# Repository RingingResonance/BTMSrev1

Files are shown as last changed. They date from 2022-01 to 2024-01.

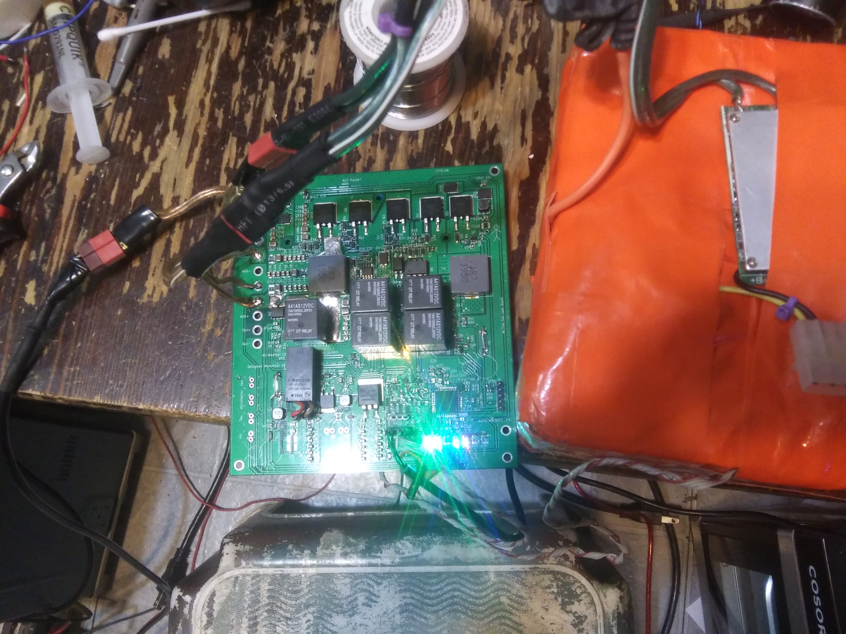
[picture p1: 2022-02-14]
pictures/20220212_222504.jpg

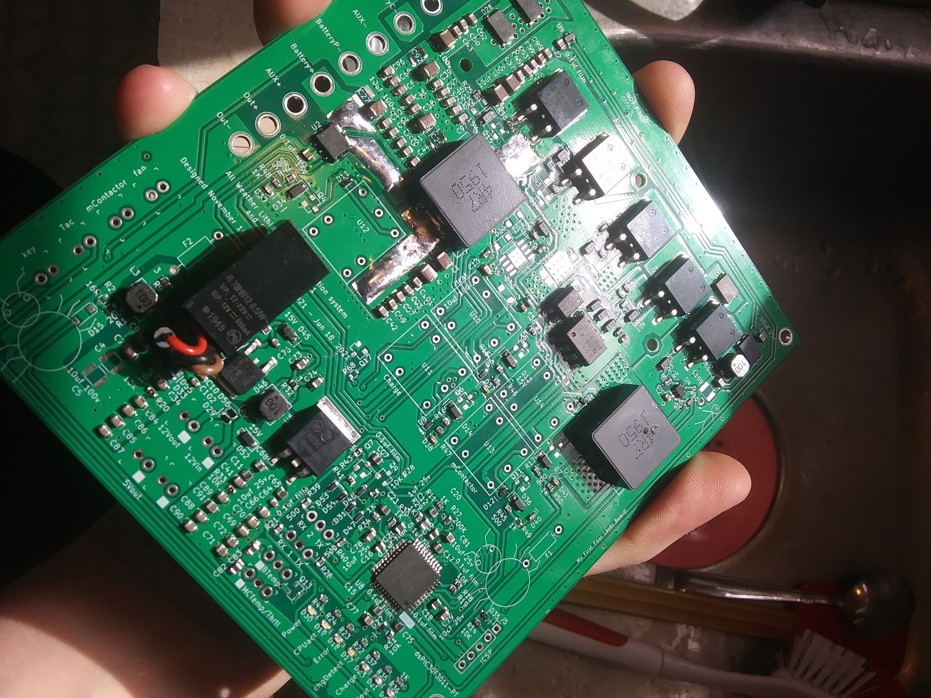
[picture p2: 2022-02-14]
pictures/20220122_115344.jpg

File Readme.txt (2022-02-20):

Battery Charge/Discharge and Heater Controller for small electric vehicles.

This system provides Battery telemetry services such as Voltage, Current, and Temperature. 

It also regulates charge/discharge voltages, limits current when battery temps are too high or too low, controls a battery heater for cold environments, and basic cooling fan control.
Works with lithium ion batteries, but does not provide cell ballancing. That must be done with a dedicated BMS.
The circuit provided should handle up to 30 amps with proper cooling. It also does basic error logging and will shut down the system on events such as under/over voltage, over current, temps out of range, internal CPU errors, etc. with room to expand.

At this time, Feb 19, 2022, Testing and verifying operation of circuit and firmware. System seems to be working as intended, but I'm still working on features and a few bugs here and there.

Heater circuit needs a higher current inductor to prevent smoke release.

Output side MOSFET drive circuit needs some fine tuning for effecientcy, but otherwise works and has been tested up to 1300 watts a few times on a 15min ride.

Charge circuit seems to work as intended, but all relays need bigger start capacitors, or better start circuits to succesfully latch.

Firmware needs display and monitoring routines written and reimplemented, and needs refactoring of several routines such as but not limited to the regulation routine for the purpose of saving code space, speed, and readability.

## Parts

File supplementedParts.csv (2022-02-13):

Index | Quantity | Part Number | Manufacturer Part Number | Description | Customer Reference | Available | Backorder | Unit Price | Extended Price USD
1 | 2 | 296-21435-5-ND | UCC27201D | IC GATE DRVR HALF-BRIDGE 8SOIC |  | 0 | 2 | 2.93000 | 5.86
2 | 10 | 846-BSS138BKWT106CT-ND | BSS138BKWT106 | NCH 60V 380MA, SOT-323, SMALL SI |  | 10 | 0 | 0.32600 | 3.26
3 | 4 | 1801-TSM3401CXRFGCT-ND | TSM3401CX RFG | MOSFET P-CHANNEL 30V 3A SOT23 |  | 4 | 0 | 0.58000 | 2.32
4 | 4 | VEMD10940FCT-ND | VEMD10940F | PHOTODIODE 790 TO 1050 NM |  | 4 | 0 | 0.40000 | 1.60
5 | 4 | ZXTP19020DFFCT-ND | ZXTP19020DFFTA | TRANS PNP 20V 5.5A SOT23F-3 |  | 4 | 0 | 0.83000 | 3.32
6 | 10 | 3757-BAS100AS-AU_R1_000A1CT-ND | BAS100AS-AU_R1_000A1 | SOD-123, SKY |  | 10 | 0 | 0.28500 | 2.85
7 | 5 | RNCF0603DTE16K0CT-ND | RNCF0603DTE16K0 | RES 16K OHM 0.5% 1/10W 0603 |  | 5 | 0 | 0.13000 | 0.65
8 | 5 | TSPB15U100SS1GCT-ND | TSPB15U100S S1G | DIODE SCHOTTKY 100V 15A SMPC4.0 |  | 5 | 0 | 1.71000 | 8.55

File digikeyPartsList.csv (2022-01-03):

Index | Quantity | Part Number | Manufacturer Part Number | Description | Customer Reference | Available | Backorder | Unit Price | Extended Price USD
1 | 17 | PCF1126CT-ND | ECP-U1C104MA5 | CAP FILM 0.1UF 20% 16VDC 0805 |  | 17 | 0 | 0.44500 | 7.57
2 | 10 | 1276-1102-1-ND | CL10A105KA8NNNC | CAP CER 1UF 25V X5R 0603 |  | 10 | 0 | 0.03400 | 0.34
3 | 17 | 490-16266-1-ND | GRM32EC72A106KE05L | CAP CER 10UF 100V X7S 1210 |  | 0 | 17 | 1.04000 | 17.68
4 | 30 | 490-10748-1-ND | GRM21BR61E106MA73L | CAP CER 10UF 25V X5R 0805 |  | 30 | 0 | 0.17200 | 5.16
5 | 1 | 490-10918-1-ND | GRJ21BC72A105KE11L | CAP CER 1UF 100V X7S 0805 |  | 1 | 0 | 0.46000 | 0.46
6 | 2 | 311-1523-1-ND | CC0603KRX7R0BB104 | CAP CER 0.1UF 100V X7R 0603 |  | 2 | 0 | 0.18000 | 0.36
7 | 50 | 490-10918-1-ND | GRJ21BC72A105KE11L | CAP CER 1UF 100V X7S 0805 |  | 50 | 0 | 0.22480 | 11.24
8 | 18 | DDZ15-7DICT-ND | DDZ15-7 | DIODE ZENER 15V 500MW SOD123 |  | 18 | 0 | 0.22300 | 4.01
9 | 5 | FSV20100VCT-ND | FSV20100V | DIODE SCHOTTKY 100V 20A TO277-3 |  | 0 | 5 | 1.46000 | 7.30
10 | 1 | VLMB1310-GS08CT-ND | VLMB1310-GS08 | LED BLUE 0603 SMD |  | 0 | 1 | 0.47000 | 0.47
11 | 1 | 732-4978-1-ND | 150060RS75000 | LED RED CLEAR 0603 SMD |  | 1 | 0 | 0.15000 | 0.15
12 | 1 | 1516-1055-1-ND | QBLP601-IG | LED GREEN CLEAR 0603 SMD |  | 1 | 0 | 0.40000 | 0.40
13 | 1 | 516-2486-1-ND | HSMA-C120 | LED AMBER CLEAR CHIP SMD R/A |  | 1 | 0 | 0.63000 | 0.63
14 | 1 | 516-2486-1-ND | HSMA-C120 | LED AMBER CLEAR CHIP SMD R/A |  | 1 | 0 | 0.63000 | 0.63
15 | 1 | 516-2486-1-ND | HSMA-C120 | LED AMBER CLEAR CHIP SMD R/A |  | 1 | 0 | 0.63000 | 0.63
16 | 1 | 1516-1055-1-ND | QBLP601-IG | LED GREEN CLEAR 0603 SMD |  | 1 | 0 | 0.40000 | 0.40
17 | 16 | CCS15S40L3FCT-ND | CCS15S40,L3F | DIODE SCHOTTKY 40V 1.5A CST2C |  | 16 | 0 | 0.30200 | 4.83
18 | 1 | 516-2486-1-ND | HSMA-C120 | LED AMBER CLEAR CHIP SMD R/A |  | 1 | 0 | 0.63000 | 0.63
19 | 4 | 516-2486-1-ND | HSMA-C120 | LED AMBER CLEAR CHIP SMD R/A |  | 4 | 0 | 0.63000 | 2.52
20 | 10 | MBR0580-TPMSCT-ND | MBR0580-TP | DIODE SCHOTTKY 80V 500MA SOD123 |  | 0 | 10 | 0.26400 | 2.64
21 | 1 | 1740-1071-1-ND | BT151S-650R,118 | SCR 650V 12A DPAK |  | 1 | 0 | 0.83000 | 0.83
22 | 2 | SRP1770TA-4R7MCT-ND | SRP1770TA-4R7M | FIXED IND 4.7UH 25A 5.5 MOHM SMD |  | 2 | 0 | 4.75000 | 9.50
23 | 3 | 732-5519-1-ND | 74404054100 | FIXED IND 10UH 2.1A 64 MOHM SMD |  | 3 | 0 | 1.16000 | 3.48
24 | 5 | 1727-7125-1-ND | PSMN5R6-100BS,118 | MOSFET N-CH 100V 100A D2PAK |  | 0 | 5 | 3.16000 | 15.80
25 | 8 | DMN65D8L-7DICT-ND | DMN65D8L-7 | MOSFET N-CH 60V 310MA SOT23 |  | 0 | 8 | 0.19000 | 1.52
26 | 2 | FDN340PCT-ND | FDN340P | MOSFET P-CH 20V 2A SUPERSOT3 |  | 0 | 2 | 0.41000 | 0.82
27 | 3 | ZXTP2025FCT-ND | ZXTP2025FTA | TRANS PNP 50V 5A SOT23-3 |  | 0 | 3 | 0.83000 | 2.49
28 | 4 | P200KBYCT-ND | ERJ-PA3F2003V | RES SMD 200K OHM 1% 1/4W 0603 |  | 4 | 0 | 0.15000 | 0.60
29 | 4 | 541-CRCW060316K0FKEAHPCT-ND | CRCW060316K0FKEAHP | RES SMD 16K OHM 1% 1/3W 0603 |  | 0 | 4 | 0.17000 | 0.68
30 | 2 | 10-ERJ-UP3J120VCT-ND | ERJ-UP3J120V | RES 12 OHM 5% 1/4W 0603 |  | 2 | 0 | 0.16000 | 0.32
31 | 2 | 541-8.06SCT-ND | CRCW06038R06FKEAHP | RES SMD 8.06 OHM 1% 1/3W 0603 |  | 2 | 0 | 0.17000 | 0.34
32 | 12 | RHM10KDCT-ND | ESR03EZPJ103 | RES SMD 10K OHM 5% 1/4W 0603 |  | 12 | 0 | 0.08200 | 0.98
33 | 21 | RNCP0603FTD499RCT-ND | RNCP0603FTD499R | RES 499 OHM 1% 1/8W 0603 |  | 21 | 0 | 0.06100 | 1.28
34 | 17 | A130416CT-ND | CRGP0603F1K0 | RES 1K OHM 1% 1/4W 0603 |  | 17 | 0 | 0.15100 | 2.57
35 | 5 | 511-1769-1-ND | SDR03EZPJ3R0 | RES SMD 3 OHM 5% 0.3W 0603 |  | 5 | 0 | 0.10000 | 0.50
36 | 1 | 945-2445-ND | R-78HB12-0.5/W | DC/DC CONVERTER 12V 6W |  | 1 | 0 | 17.16000 | 17.16
37 | 1 | 620-1817-1-ND | ACS780LLRTR-050B-T | HIGH-PRECISION LINEAR HALL-EFFEC |  | 0 | 1 | 5.27000 | 5.27
38 | 1 | 296-31998-1-ND | UCC27201DDAR | IC GATE DRVR HALF-BRIDGE 8SOPWR |  | 0 | 1 | 2.72000 | 2.72
39 | 1 | FAN3111ESXCT-ND | FAN3111ESX | IC GATE DRVR LOW-SIDE SOT23-5 |  | 0 | 1 | 0.91000 | 0.91
40 | 1 | 516-1789-1-ND | HCPL-3120-500E | OPTOISO 3.75KV GATE DRVR 8DIP GW |  | 0 | 1 | 3.33000 | 3.33
41 | 1 | MC7805CD2TR4GOSCT-ND | MC7805CD2TR4G | IC REG LINEAR 5V 1A D2PAK |  | 1 | 0 | 0.80000 | 0.80
42 | 1 | 160-1367-5-ND | LTV-817S | OPTOISOLATR 5KV TRANSISTOR 4-SMD |  | 1 | 0 | 0.43000 | 0.43
43 | 1 | DSPIC30F301130IPT-ND | DSPIC30F3011-30I/PT | IC MCU 16BIT 24KB FLASH 44TQFP |  | 0 | 1 | 6.24000 | 6.24
44 | 1 | LM62CIM3/NOPBCT-ND | LM62CIM3/NOPB | SENSOR ANALOG 0C-90C SOT23-3 |  | 1 | 0 | 1.29000 | 1.29
45 | 5 | 2449-A41AS12VDC-ND | A41AS12VDC | RELAY AUTO SPST 12VDC PCB |  | 5 | 0 | 1.11000 | 5.55
46 | 1 | NL17SZ74USGOSCT-ND | NL17SZ74USG | IC FF D-TYPE SNGL 1BIT US8 |  | 0 | 1 | 0.47000 | 0.47
47 | 2 | 311-6.04HRCT-ND | RC0603FR-076R04L | RES 6.04 OHM 1% 1/10W 0603 |  | 2 | 0 | 0.10000 | 0.20

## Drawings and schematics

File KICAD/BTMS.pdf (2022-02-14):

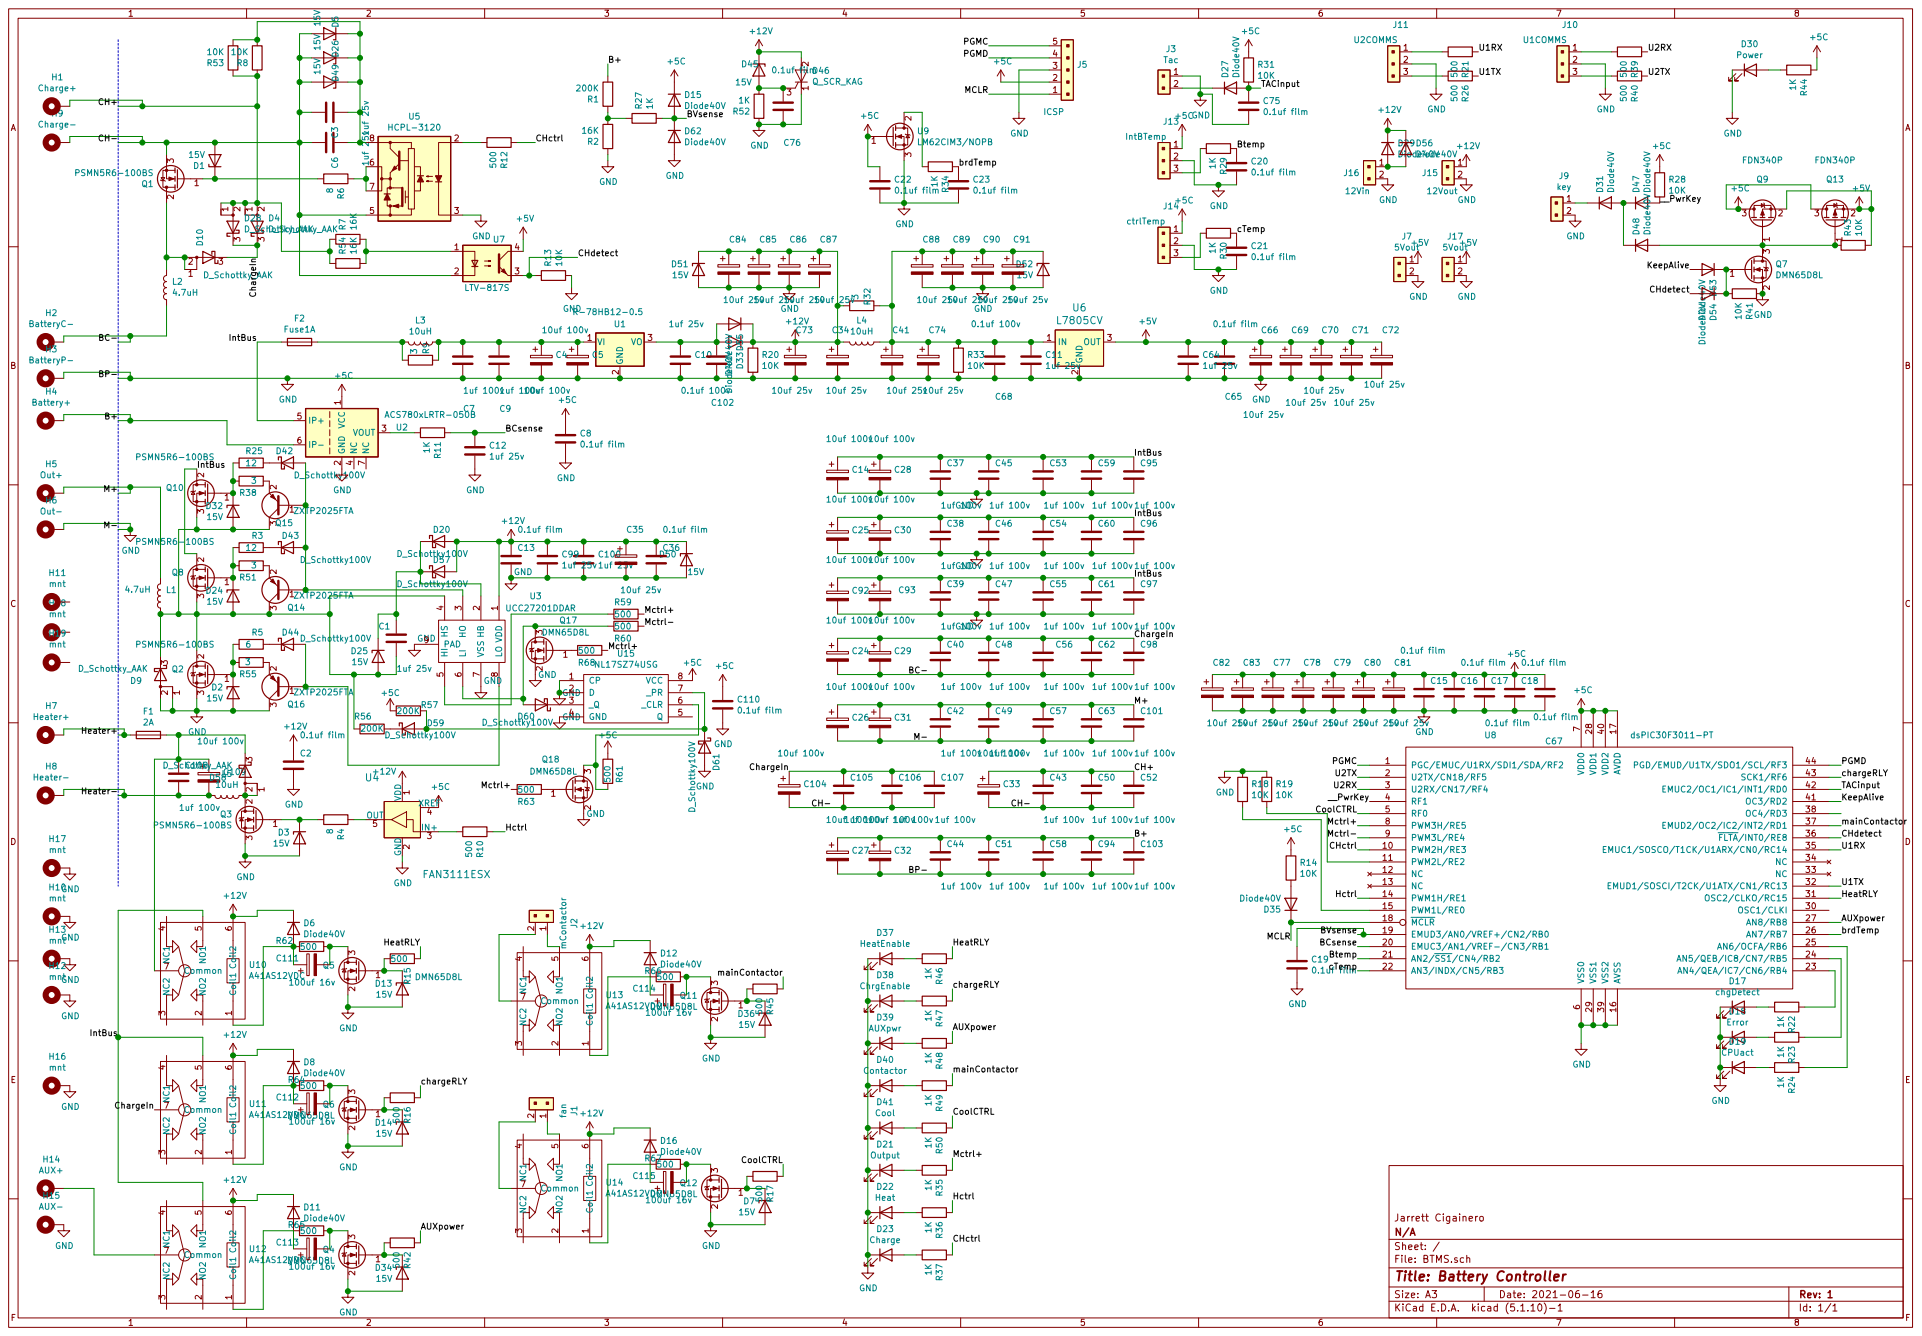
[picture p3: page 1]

Jarrett Cigainero
Id: 1/1 Title: Battery Controller File: BTMS.sch Sheet: / N/A

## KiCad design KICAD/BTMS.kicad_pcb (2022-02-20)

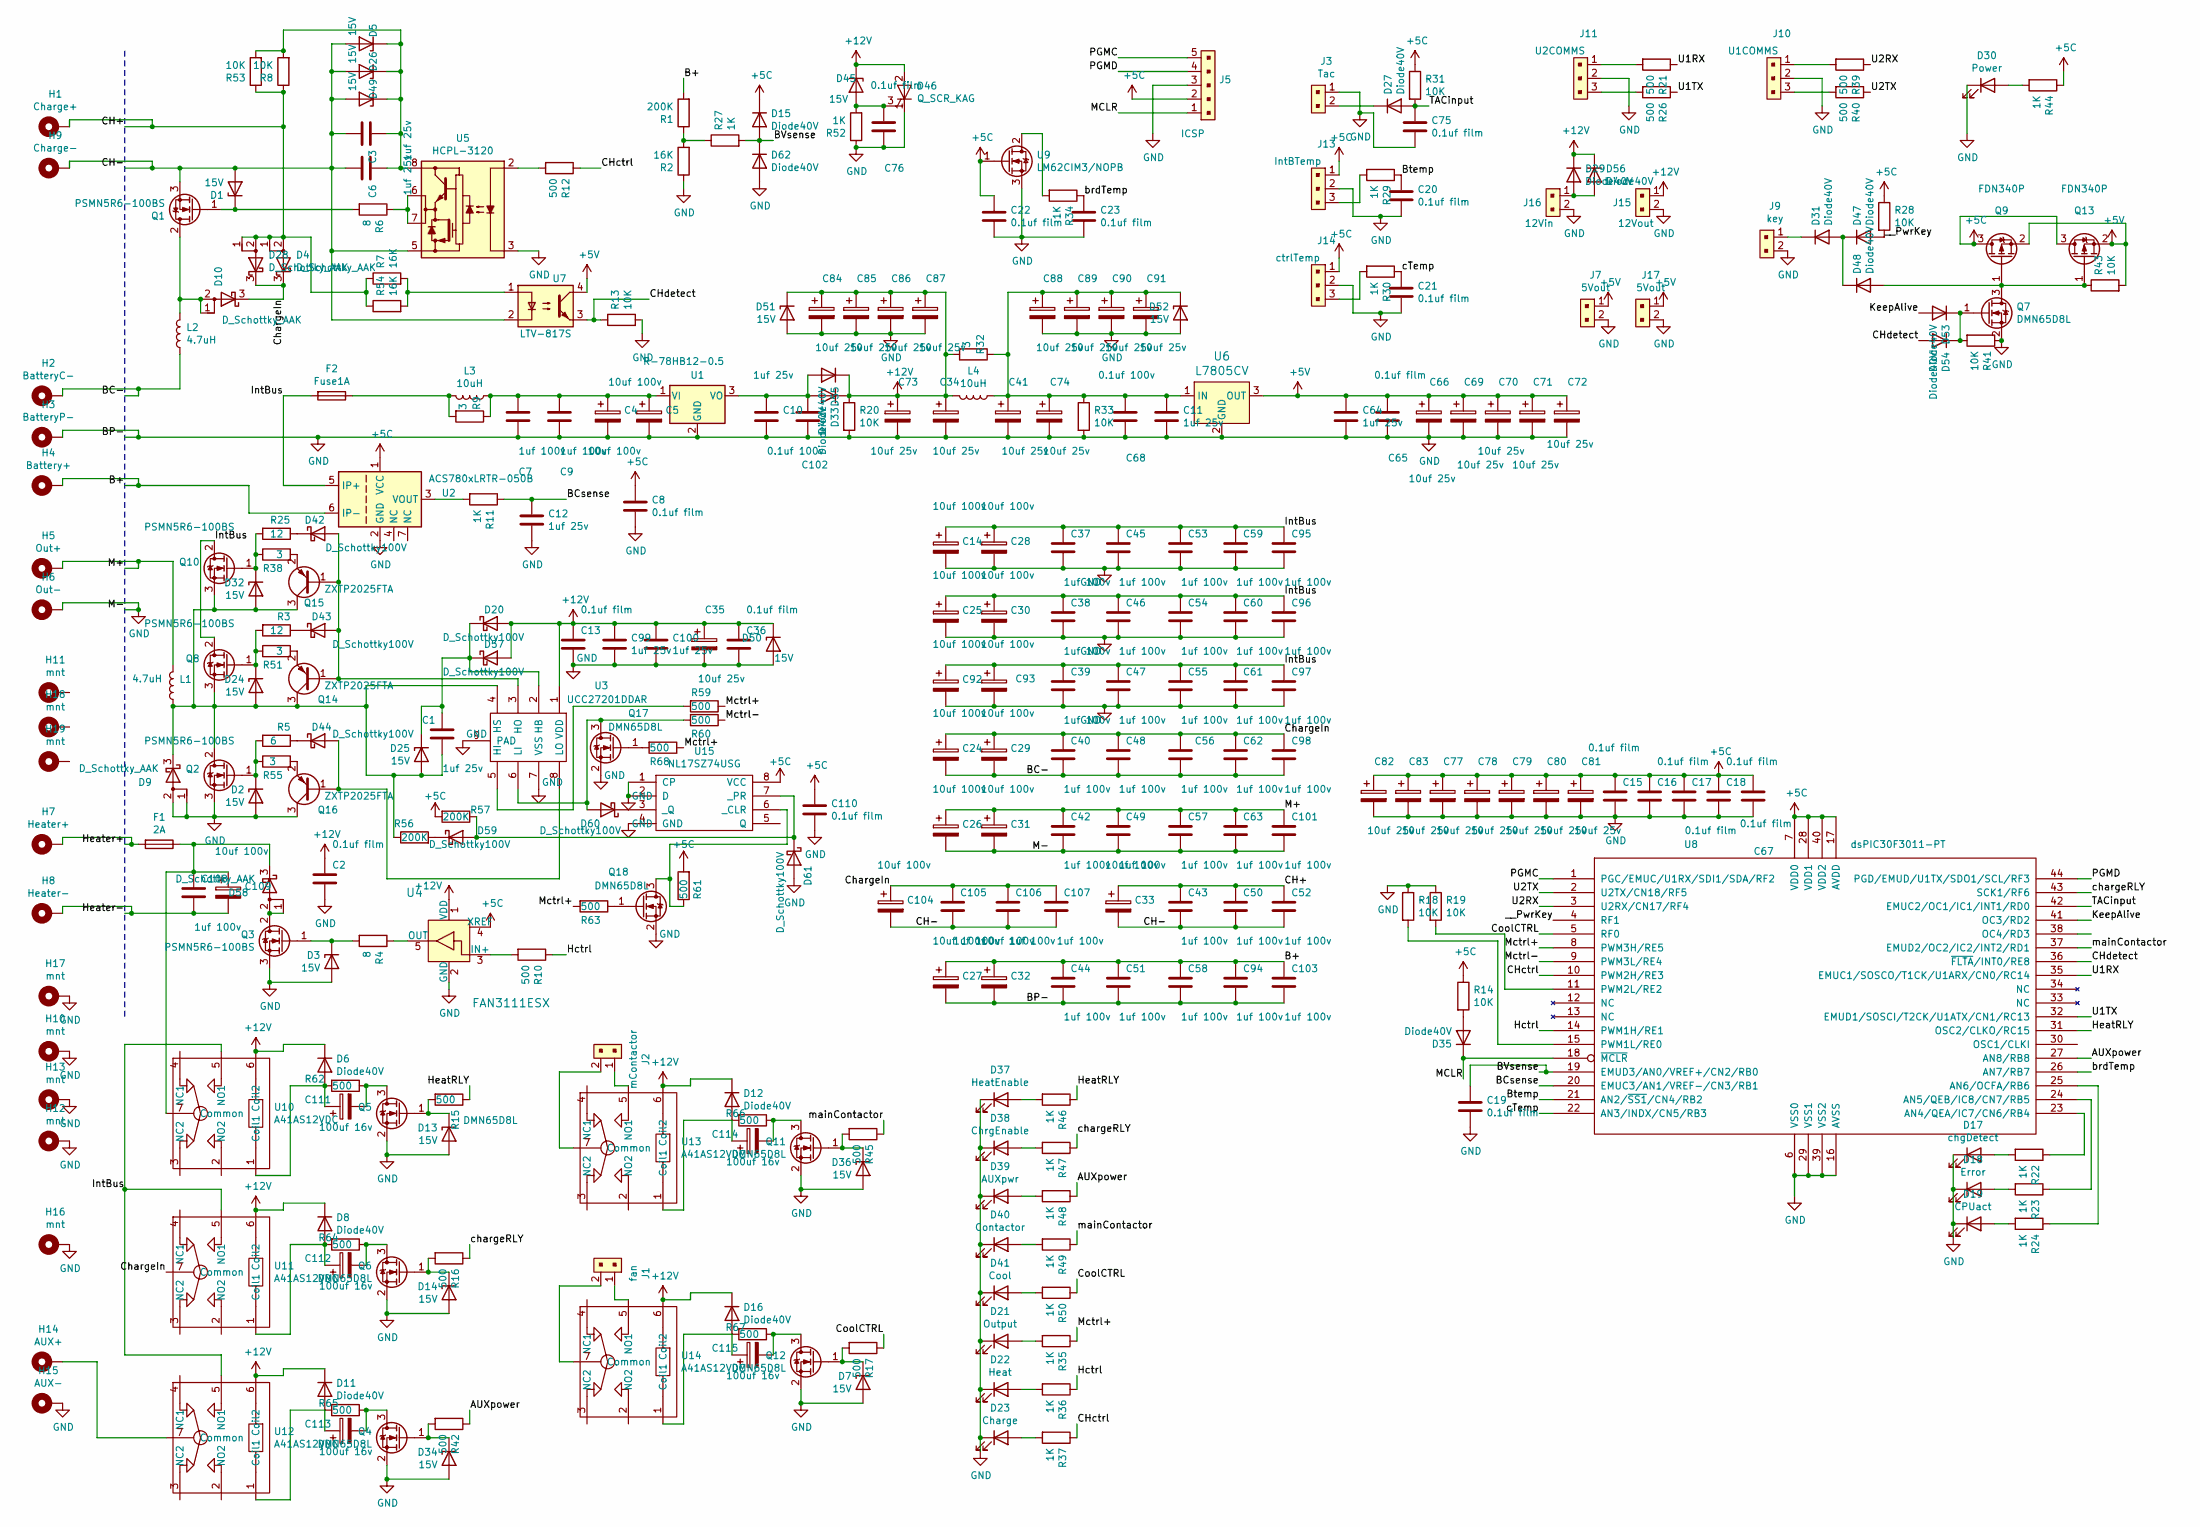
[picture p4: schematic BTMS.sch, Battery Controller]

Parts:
C1, C3, C6, C10, C11, C12, C64, C99, C100: 1uf 25v; C_0603; Digi-Key_PN 1276-1102-1-ND
C2, C8, C13, C15, C16, C17, C18, C19, C20, C21, C22, C23, C36, C65, C75, C76, C110: 0.1uf film; C_0603; Digi-Key_PN PCF1126CT-ND
C4, C5, C14, C24, C25, C26, C27, C28, C29, C30, C31, C32, C33, C92, C93, C104, C109: 10uf 100v; C_1210; Digi-Key_PN 490-16266-1-ND
C7, C9, C37, C38, C39, C40, C42, C43, C44, C45, C46, C47, C48, C49, C50, C51, C52, C53, C54, C55, C56, C57, C58, C59, C60, C61, C62, C63, C94, C95, C96, C97, C98, C101, C103, C105, C106, C107, C108: 1uf 100v; C_0805; Digi-Key_PN 490-10918-1-ND
C34, C35, C41, C66, C69, C70, C71, C72, C73, C74, C77, C78, C79, C80, C81, C82, C83, C84, C85, C86, C87, C88, C89, C90, C91: 10uf 25v; C_0805; Digi-Key_PN 490-10748-1-ND
C67: 0.1uf film; C_0805; Digi-Key_PN 490-10918-1-ND
C68, C102: 0.1uf 100v; C_0603; Digi-Key_PN 311-1523-1-ND
C111, C112, C113, C114, C115: 100uf 16v; CP_Elec_6.3x5.7; Digi-Key_PN 1572-1239-1-ND
D1, D2, D3, D5, D7, D13, D14, D24, D25, D26, D32, D34, D36, D45, D49, D50, D51, D52: 15V; D_SOD-123; Digi-Key_PN DDZ15-7DICT-ND
D4, D9, D10, D28, D58: D_Schottky_AAK; TO-277A; Digi-Key_PN FSV20100VCT-ND
D6, D8, D11, D12, D15, D16, D27, D29, D31, D33, D35, D47, D48, D53, D54, D55, D56, D62: Diode40V; D_0603; Digi-Key_PN CCS15S40L3FCT-ND
D17: chgDetect; LED_0603; Digi-Key_PN VLMB1310-GS08CT-ND
D18: Error; LED_0603; Digi-Key_PN 732-4978-1-ND
D19: CPUact; LED_0603; Digi-Key_PN 1516-1055-1-ND
D20, D42, D43, D44, D57, D59, D60, D61: D_Schottky100V; D_SOD-123; Digi-Key_PN MBR0580-TPMSCT-ND
D21: Output; LED_0603; Digi-Key_PN 516-2486-1-ND
D22: Heat; LED_0603; Digi-Key_PN 516-2486-1-ND
D23: Charge; LED_0603; Digi-Key_PN 516-2486-1-ND
D30: Power; LED_0603; Digi-Key_PN 1516-1055-1-ND
D37: HeatEnable; LED_0603; Digi-Key_PN 516-2486-1-ND
D38: ChrgEnable; LED_0603; Digi-Key_PN 516-2486-1-ND
D39: AUXpwr; LED_0603; Digi-Key_PN 516-2486-1-ND
D40: Contactor; LED_0603; Digi-Key_PN 516-2486-1-ND
D41: Cool; LED_0603; Digi-Key_PN 516-2486-1-ND
D46: Q_SCR_KAG; TO-252-2; Digi-Key_PN 1740-1071-1-ND
F1: 2A; R_Axial_DIN0207_L6.3mm_D2.5mm_P10.16mm_Horizontal
F2: Fuse1A; R_Axial_DIN0207_L6.3mm_D2.5mm_P10.16mm_Horizontal
H1: Charge+; 1pin
H2: BatteryC-; 1pin
H3: BatteryP-; 1pin
H4: Battery+; 1pin
H5: Out+; 1pin
H6: Out-; 1pin
H7: Heater+; 1pin
H8: Heater-; 1pin
H9: Charge-; 1pin
H10, H12, H13, H16, H17: mnt; 1pin
H11, H18, H19: mnt; MountingHole_2.7mm
H14: AUX+; 1pin
H15: AUX-; 1pin
J1: fan; PinHeader_1x2_P2.54mm_Drill1.02mm; MPN 22-23-2021
J2: mContactor; PinHeader_1x2_P2.54mm_Drill1.02mm; MPN 22-23-2021
J3: Tac; PinHeader_1x2_P2.54mm_Drill1.02mm; MPN 22-23-2021
J5: ICSP; Pin_Header_Straight_1x05_Pitch2.54mm; MPN B5B-XH-A(LF)(SN)
J7, J17: 5Vout; PinHeader_1x2_P2.54mm_Drill1.02mm; MPN 22-23-2021
J9: key; PinHeader_1x2_P2.54mm_Drill1.02mm; MPN 22-23-2021
J10: U1COMMS; PinHeader_1x3_P2.54_Drill1.1mm; MPN 640456-3
J11: U2COMMS; PinHeader_1x3_P2.54_Drill1.1mm; MPN 640456-3
J13: IntBTemp; PinHeader_1x3_P2.54_Drill1.1mm; MPN 640456-3
J14: ctrlTemp; PinHeader_1x3_P2.54_Drill1.1mm; MPN 640456-3
J15: 12Vout; PinHeader_1x2_P2.54mm_Drill1.02mm; MPN 22-23-2021
J16: 12Vin; PinHeader_1x2_P2.54mm_Drill1.02mm; MPN 22-23-2021
L1, L2: 4.7uH; Inductor_Wurth_HCI-1890; Digi-Key_PN SRP1770TA-4R7MCT-ND
L3, L4: 10uH; Inductor_Wurth_HCI-5040; Digi-Key_PN 732-5519-1-ND
Q1, Q2, Q3, Q8, Q10: PSMN5R6-100BS; TO-263-2; Digi-Key_PN 1727-7125-1-ND
Q4, Q5, Q6, Q7, Q11, Q12, Q17, Q18: DMN65D8L; SOT-23; Digi-Key_PN DMN65D8L-7DICT-ND
Q9, Q13: FDN340P; SOT-23; Digi-Key_PN FDN340PCT-ND
Q14, Q15, Q16: ZXTP2025FTA; SOT-23; Digi-Key_PN ZXTP2025FCT-ND
R1, R56, R57: 200K; R_0603; Digi-Key_PN P200KBYCT-ND
R2, R7, R54: 16K; R_0603; Digi-Key_PN 541-CRCW060316K0FKEAHPCT-ND
R3, R25: 12; R_0603; Digi-Key_PN 10-ERJ-UP3J120VCT-ND
R4, R6: 8; R_0603; Digi-Key_PN 541-8.06SCT-ND
R5: 6; R_0603; Digi-Key_PN 311-6.04HRCT-ND
R8, R13, R14, R18, R19, R20, R28, R31, R33, R41, R43, R53: 10K; R_0603; Digi-Key_PN RHM10KDCT-ND
R9, R32, R38, R51, R55: 3; R_0603; Digi-Key_PN 511-1769-1-ND
R10, R12, R15, R16, R17, R21, R26, R39, R40, R42, R45, R59, R60, R61, R62, R63, R64, R65, R66, R67, R68: 500; R_0603; Digi-Key_PN RNCP0603FTD499RCT-ND
R11, R22, R23, R24, R27, R29, R30, R34, R35, R36, R37, R44, R46, R47, R48, R49, R50, R52: 1K; R_0603; Digi-Key_PN A130416CT-ND
U1: R-78HB12-0.5; TO-220-3_Horizontal; Digi-Key_PN 945-2445-ND
U2: ACS780xLRTR-050B; Allegro_PSOF-7_4.8x6.4mm_P1.60mm; Digi-Key_PN 620-1817-1-ND
U3: UCC27201DDAR; TI_SO-PowerPAD-8_ThermalVias; Digi-Key_PN 296-31998-1-ND
U4: FAN3111ESX; SOT-753; MPN FAN3111ESX; Digi-Key_PN FAN3111ESXCT-ND
U5: HCPL-3120; DIP-8_SMD; Digi-Key_PN 516-1789-1-ND
U6: L7805CV; TO-263-2; MPN L7805CV; Digi-Key_PN MC7805CD2TR4GOSCT-ND
U7: LTV-817S; SO-4_7.6x3.6mm_Pitch2.54mm; Digi-Key_PN 160-1367-5-ND
U8: dsPIC30F3011-PT; TQFP-44_10x10mm; Digi-Key_PN DSPIC30F301130IPT-ND
U9: LM62CIM3/NOPB; SOT-23; Digi-Key_PN LM62CIM3/NOPBCT-ND
U10, U11, U12, U13, U14: A41AS12VDC; A4series; Digi-Key_PN 2449-A41AS12VDC-ND
U15: NL17SZ74USG; SOT-23-8_Handsoldering; Digi-Key_PN NL17SZ74USGOSCT-ND

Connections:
+5C: C8.1, C15.1, C16.1, C17.1, C18.1, C22.1, C67.1, C77.1, C78.1, C79.1, C80.1, C81.1, C82.1, C83.1, C110.1, D15.1 (K), J5.2, J13.1, J14.1, Q9.3 (D), Q13.3 (D), R14.1, R28.1, R31.1, R44.1, R57.2, R61.2, U2.1 (VCC), U4.4 (XREF), U8.7 (VDD0), U8.17 (AVDD), U8.28 (VDD1), U8.40 (VDD2), U9.1 (G), U15.8 (VCC)
+5V: C64.1, C65.1, C66.1, C69.1, C70.1, C71.1, C72.1, J7.1, J17.1, Q9.2 (S), Q13.2 (S), R43.2, U6.3 (OUT), U7.4
+12V: C2.1, C13.1, C34.1, C35.1, C36.1, C73.1, C84.1, C85.1, C86.1, C87.1, C99.1, C100.1, D6.1 (K), D8.1 (K), D11.1 (K), D12.1 (K), D16.1 (K), D20.2 (A), D29.1 (K), D33.1 (K), D45.1 (K), D46.2 (A), D50.1 (K), D51.1 (K), D55.1 (K), D56.1 (K), D57.2 (A), J15.1, L4.2, R20.1, R32.2, U3.1 (VDD), U4.1 (VDD), U10.6 (Coil2), U11.6 (Coil2), U12.6 (Coil2), U13.6 (Coil2), U14.6 (Coil2)
/AUXpower: R42.1, R48.1, U8.27 (AN8/RB8)
/B+: C27.1, C32.1, C44.1, C51.1, C58.1, C94.1, C103.1, H4.1, R1.2, U2.6 (IP-)
/BC-: C24.2, C29.2, C40.2, C48.2, C56.2, C62.2, C98.2, H2.1, L2.1
/BCsense: C12.1, R11.1, U8.20 (EMUC3/AN1/VREF-/CN3/RB1)
/BVsense: C19.1, D15.2 (A), D62.1 (K), R27.2, U8.19 (EMUD3/AN0/VREF+/CN2/RB0)
/Btemp: C20.1, R29.1, U8.21 (AN2/~SS1~/CN4/RB2)
/CH+: C33.1, C43.1, C50.1, C52.1, D4.1 (A), D4.2 (A), D28.1 (A), D28.2 (A), H1.1, R7.1, R8.1, R53.1, R54.1
/CH-: C3.2, C6.2, C33.2, C43.2, C50.2, C52.2, C104.2, C105.2, C106.2, C107.2, D1.2 (A), D5.2 (A), D26.2 (A), D49.2 (A), H9.1, Q1.3 (S), U5.5 (VEE), U7.2
/CHctrl: R12.1, R37.1, U8.10 (PWM2H/RE3)
/CHdetect: D54.2 (A), R13.1, U7.3, U8.36 (~FLTA~/INT0/RE8)
/ChargeIn: C24.1, C29.1, C40.1, C48.1, C56.1, C62.1, C98.1, C104.1, C105.1, C106.1, C107.1, D4.3 (K), D10.3 (K), D28.3 (K), U11.7 (Common)
/CoolCTRL: R17.1, R50.1, U8.5 (RF0)
/Hctrl: R10.1, R36.1, U8.14 (PWM1H/RE1)
/HeatRLY: R15.1, R46.1, U8.31 (OSC2/CLKO/RC15)
/Heater+: F1.2, H7.1
/Heater-: C108.2, C109.2, H8.1
/IntBus: C14.1, C25.1, C28.1, C30.1, C37.1, C38.1, C39.1, C45.1, C46.1, C47.1, C53.1, C54.1, C55.1, C59.1, C60.1, C61.1, C92.1, C93.1, C95.1, C96.1, C97.1, F2.2, Q8.2 (D), Q10.2 (D), U2.5 (IP+), U10.5 (NO1), U11.5 (NO1), U12.5 (NO1)
/KeepAlive: D53.2 (A), U8.41 (OC3/RD2)
/M+: C26.1, C31.1, C42.1, C49.1, C57.1, C63.1, C101.1, H5.1, L1.2
/MCLR: D35.1 (K), J5.1, U8.18 (~MCLR~)
/Mctrl+: R35.1, R59.1, R63.2, R68.1, U8.8 (PWM3H/RE5)
/Mctrl-: R60.1, U8.9 (PWM3L/RE4)
/PGMC: J5.5, U8.1 (PGC/EMUC/U1RX/SDI1/SDA/RF2)
/PGMD: J5.4, U8.44 (PGD/EMUD/U1TX/SDO1/SCL/RF3)
/TACinput: C75.1, D27.2 (A), R31.2, U8.42 (EMUC2/OC1/IC1/INT1/RD0)
/U1RX: R21.1, U8.35 (EMUC1/SOSCO/T1CK/U1ARX/CN0/RC14)
/U1TX: R26.1, U8.32 (EMUD1/SOSCI/T2CK/U1ATX/CN1/RC13)
/U2RX: R39.1, U8.3 (U2RX/CN17/RF4)
/U2TX: R40.1, U8.2 (U2TX/CN18/RF5)
/__PwrKey: D47.2 (A), R28.2, U8.4 (RF1)
/brdTemp: C23.1, R34.1, U8.26 (AN7/RB7)
/cTemp: C21.1, R30.1, U8.22 (AN3/INDX/CN5/RB3)
/chargeRLY: R16.1, R47.1, U8.43 (SCK1/RF6)
/mainContactor: R45.1, R49.1, U8.37 (EMUD2/OC2/IC2/INT2/RD1)
GND: C2.2, C4.2, C5.2, C7.2, C8.2, C9.2, C10.2, C11.2, C12.2, C13.2, C14.2, C15.2, C16.2, C17.2, C18.2, C19.2, C20.2, C21.2, C22.2, C23.2, C25.2, C26.2, C27.2, C28.2, C30.2, C31.2, C32.2, C34.2, C35.2, C36.2, C37.2, C38.2, C39.2, C41.2, C42.2, C44.2, C45.2, C46.2, C47.2, C49.2, C51.2, C53.2, C54.2, C55.2, C57.2, C58.2, C59.2, C60.2, C61.2, C63.2, C64.2, C65.2, C66.2, C67.2, C68.2, C69.2, C70.2, C71.2, C72.2, C73.2, C74.2, C75.2, C76.2, C77.2, C78.2, C79.2, C80.2, C81.2, C82.2, C83.2, C84.2, C85.2, C86.2, C87.2, C88.2, C89.2, C90.2, C91.2, C92.2, C93.2, C94.2, C95.2, C96.2, C97.2, C99.2, C100.2, C101.2, C102.2, C103.2, C110.2, D2.2 (A), D3.2 (A), D7.2 (A), D9.1 (A), D9.2 (A), D13.2 (A), D14.2 (A), D17.1 (K), D18.1 (K), D19.1 (K), D21.1 (K), D22.1 (K), D23.1 (K), D30.1 (K), D34.2 (A), D36.2 (A), D37.1 (K), D38.1 (K), D39.1 (K), D40.1 (K), D41.1 (K), D46.1 (K), D50.2 (A), D51.2 (A), D52.2 (A), D61.2 (A), D62.2 (A), H3.1, H6.1, H10.1, H12.1, H13.1, H15.1, H16.1, H17.1, J3.1, J5.3, J7.2, J9.2, J10.2, J11.2, J13.2, J14.2, J15.2, J16.2, J17.2, Q2.3 (S), Q3.3 (S), Q4.2 (S), Q5.2 (S), Q6.2 (S), Q7.2 (S), Q11.2 (S), Q12.2 (S), Q16.3 (C), Q17.2 (S), Q18.2 (S), R2.1, R13.2, R18.1, R19.1, R20.2, R33.2, R41.1, R52.1, U1.2 (GND), U2.2 (GND), U3.7 (VSS), U3.9 (PAD), U4.2 (GND), U5.3 (C), U6.2 (GND), U8.6 (VSS0), U8.16 (AVSS), U8.29 (VSS1), U8.39 (VSS2), U9.3 (S), U15.1 (CP), U15.2 (D), U15.4 (GND)
unnamed: C1.1, D20.1 (K), D25.1 (K), D57.1 (K), U3.2 (HB)
unnamed: C1.2, D9.3 (K), D24.2 (A), D25.2 (A), D32.2 (A), L1.1, Q2.2 (D), Q8.3 (S), Q10.3 (S), Q14.3 (C), Q15.3 (C), R56.1, U3.4 (HS)
unnamed: C3.1, C6.1, D5.1 (K), D26.1 (K), D49.1 (K), R8.2, R53.2, U5.8 (VCC)
unnamed: C4.1, C5.1, C7.1, C9.1, L3.1, R9.1, U1.1 (VI)
unnamed: C10.1, C102.1, D33.2 (A), D55.2 (A), U1.3 (VO)
unnamed: C11.1, C41.1, C68.1, C74.1, C88.1, C89.1, C90.1, C91.1, D52.1 (K), L4.1, R32.1, R33.1, U6.1 (IN)
unnamed: C76.1, D45.2 (A), D46.3 (G), R52.2
unnamed: C108.1, C109.1, D58.3 (K), F1.1, U10.7 (Common)
unnamed: C111.1, D6.2 (A), R62.2, U10.1 (Coil1)
unnamed: C111.2, Q5.3 (D), R62.1
unnamed: C112.1, D8.2 (A), R64.2, U11.1 (Coil1)
unnamed: C112.2, Q6.3 (D), R64.1
unnamed: C113.1, D11.2 (A), R65.2, U12.1 (Coil1)
unnamed: C113.2, Q4.3 (D), R65.1
unnamed: C114.1, D12.2 (A), R66.2, U13.1 (Coil1)
unnamed: C114.2, Q11.3 (D), R66.1
unnamed: C115.1, D16.2 (A), R67.2, U14.1 (Coil1)
unnamed: C115.2, Q12.3 (D), R67.1
unnamed: D1.1 (K), Q1.1 (G), R6.2
unnamed: D2.1 (K), Q2.1 (G), R5.2, R55.1
unnamed: D3.1 (K), Q3.1 (G), R4.2
unnamed: D7.1 (K), Q12.1 (G), R17.2
unnamed: D10.1 (A), D10.2 (A), L2.2, Q1.2 (D)
unnamed: D13.1 (K), Q5.1 (G), R15.2
unnamed: D14.1 (K), Q6.1 (G), R16.2
unnamed: D17.2 (A), R22.2
unnamed: D18.2 (A), R23.2
unnamed: D19.2 (A), R24.2
unnamed: D21.2 (A), R35.2
unnamed: D22.2 (A), R36.2
unnamed: D23.2 (A), R37.2
unnamed: D24.1 (K), Q8.1 (G), R3.2, R51.1
unnamed: D27.1 (K), J3.2
unnamed: D29.2 (A), D56.2 (A), J16.1
unnamed: D30.2 (A), R44.2
unnamed: D31.1 (K), J9.1
unnamed: D31.2 (A), D47.1 (K), D48.1 (K)
unnamed: D32.1 (K), Q10.1 (G), R25.2, R38.1
unnamed: D34.1 (K), Q4.1 (G), R42.2
unnamed: D35.2 (A), R14.2
unnamed: D36.1 (K), Q11.1 (G), R45.2
unnamed: D37.2 (A), R46.2
unnamed: D38.2 (A), R47.2
unnamed: D39.2 (A), R48.2
unnamed: D40.2 (A), R49.2
unnamed: D41.2 (A), R50.2
unnamed: D42.1 (K), R25.1
unnamed: D42.2 (A), D43.2 (A), Q14.1 (B), Q15.1 (B), U3.3 (HO)
unnamed: D43.1 (K), R3.1
unnamed: D44.1 (K), R5.1
unnamed: D44.2 (A), Q16.1 (B), U3.8 (LO)
unnamed: D48.2 (A), Q7.3 (D), Q9.1 (G), Q13.1 (G), R43.1
unnamed: D53.1 (K), D54.1 (K), Q7.1 (G), R41.2
unnamed: D58.1 (A), D58.2 (A), Q3.2 (D)
unnamed: D59.1 (K), R56.2
unnamed: D59.2 (A), D61.1 (K), R57.1, U15.7 (_PR)
unnamed: D60.1 (K), U15.3 (_Q)
unnamed: D60.2 (A), Q17.3 (D), R60.2, U3.6 (LI)
unnamed: F2.1, L3.2, R9.2
unnamed: H14.1, U12.7 (Common)
unnamed: J1.1, U14.5 (NO1)
unnamed: J1.2, U14.7 (Common)
unnamed: J2.1, U13.5 (NO1)
unnamed: J2.2, U13.7 (Common)
unnamed: J10.1, R39.2
unnamed: J10.3, R40.2
unnamed: J11.1, R21.2
unnamed: J11.3, R26.2
unnamed: J13.3, R29.2
unnamed: J14.3, R30.2
unnamed: Q14.2 (E), R51.2
unnamed: Q15.2 (E), R38.2
unnamed: Q16.2 (E), R55.2
unnamed: Q17.1 (G), R68.2
unnamed: Q18.1 (G), R63.1
unnamed: Q18.3 (D), R61.1, U15.6 (_CLR)
unnamed: R1.1, R2.2, R27.1
unnamed: R4.1, U4.5 (OUT)
unnamed: R6.1, U5.6 (VO), U5.7 (VO)
unnamed: R10.2, U4.3 (IN+)
unnamed: R11.2, U2.3 (VOUT)
unnamed: R12.2, U5.2 (A)
unnamed: R18.2, U8.15 (PWM1L/RE0)
unnamed: R19.2, U8.11 (PWM2L/RE2)
unnamed: R22.1, U8.23 (AN4/QEA/IC7/CN6/RB4)
unnamed: R23.1, U8.24 (AN5/QEB/IC8/CN7/RB5)
unnamed: R24.1, U8.25 (AN6/OCFA/RB6)
unnamed: R34.2, U9.2 (D)
unnamed: R7.2, R54.2, U7.1
unnamed: R59.2, U3.5 (HI)

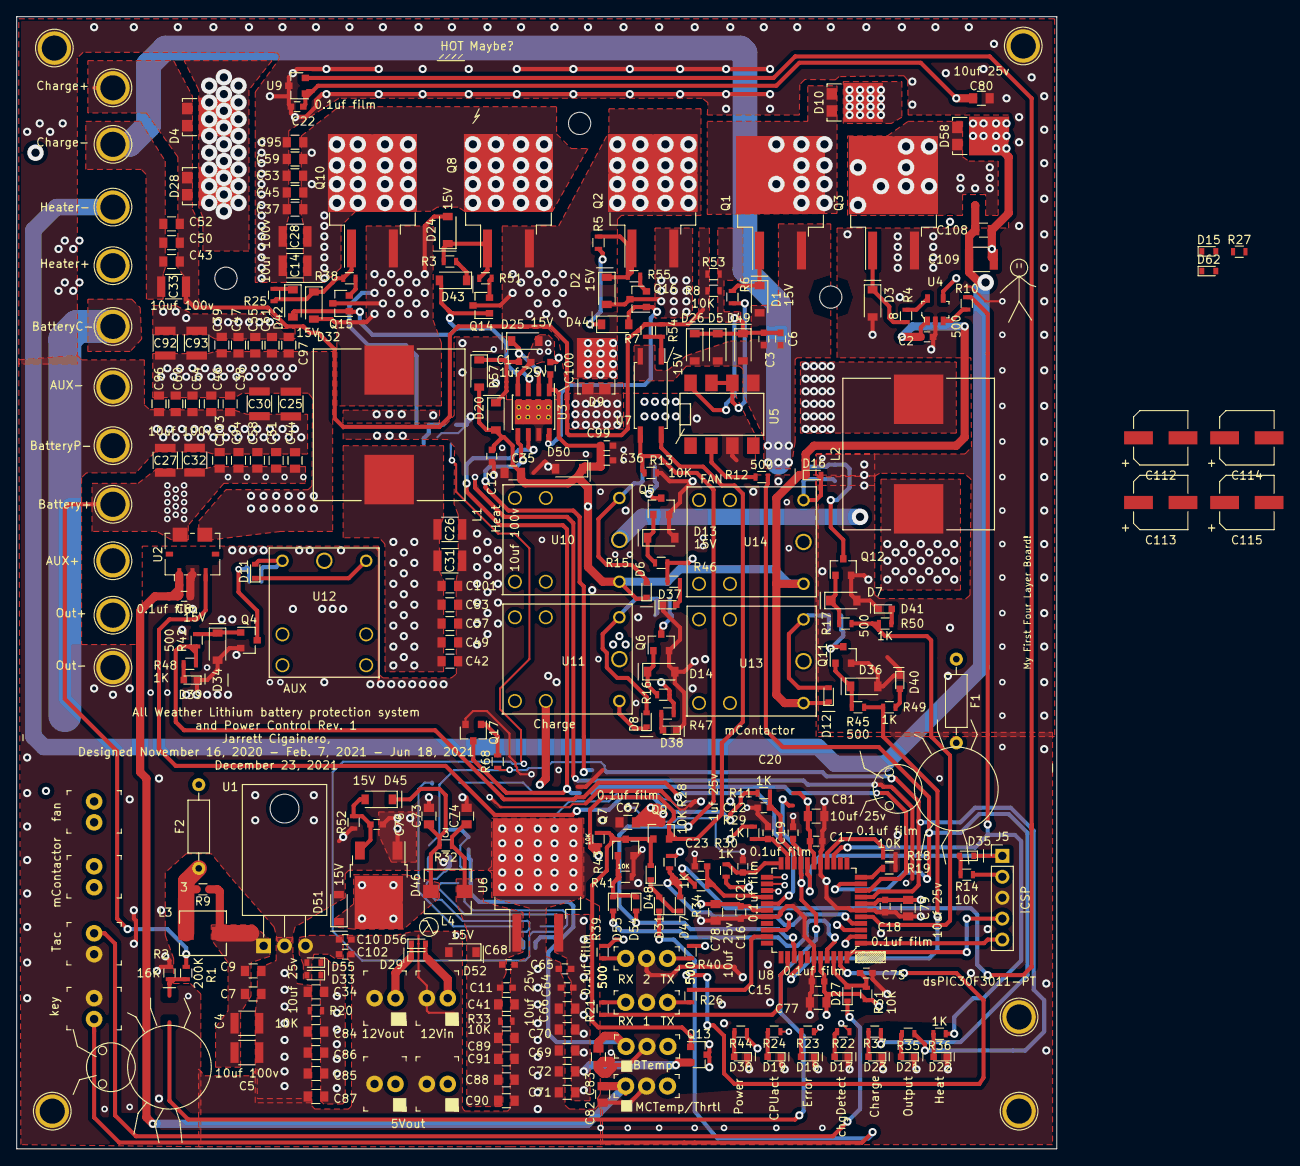
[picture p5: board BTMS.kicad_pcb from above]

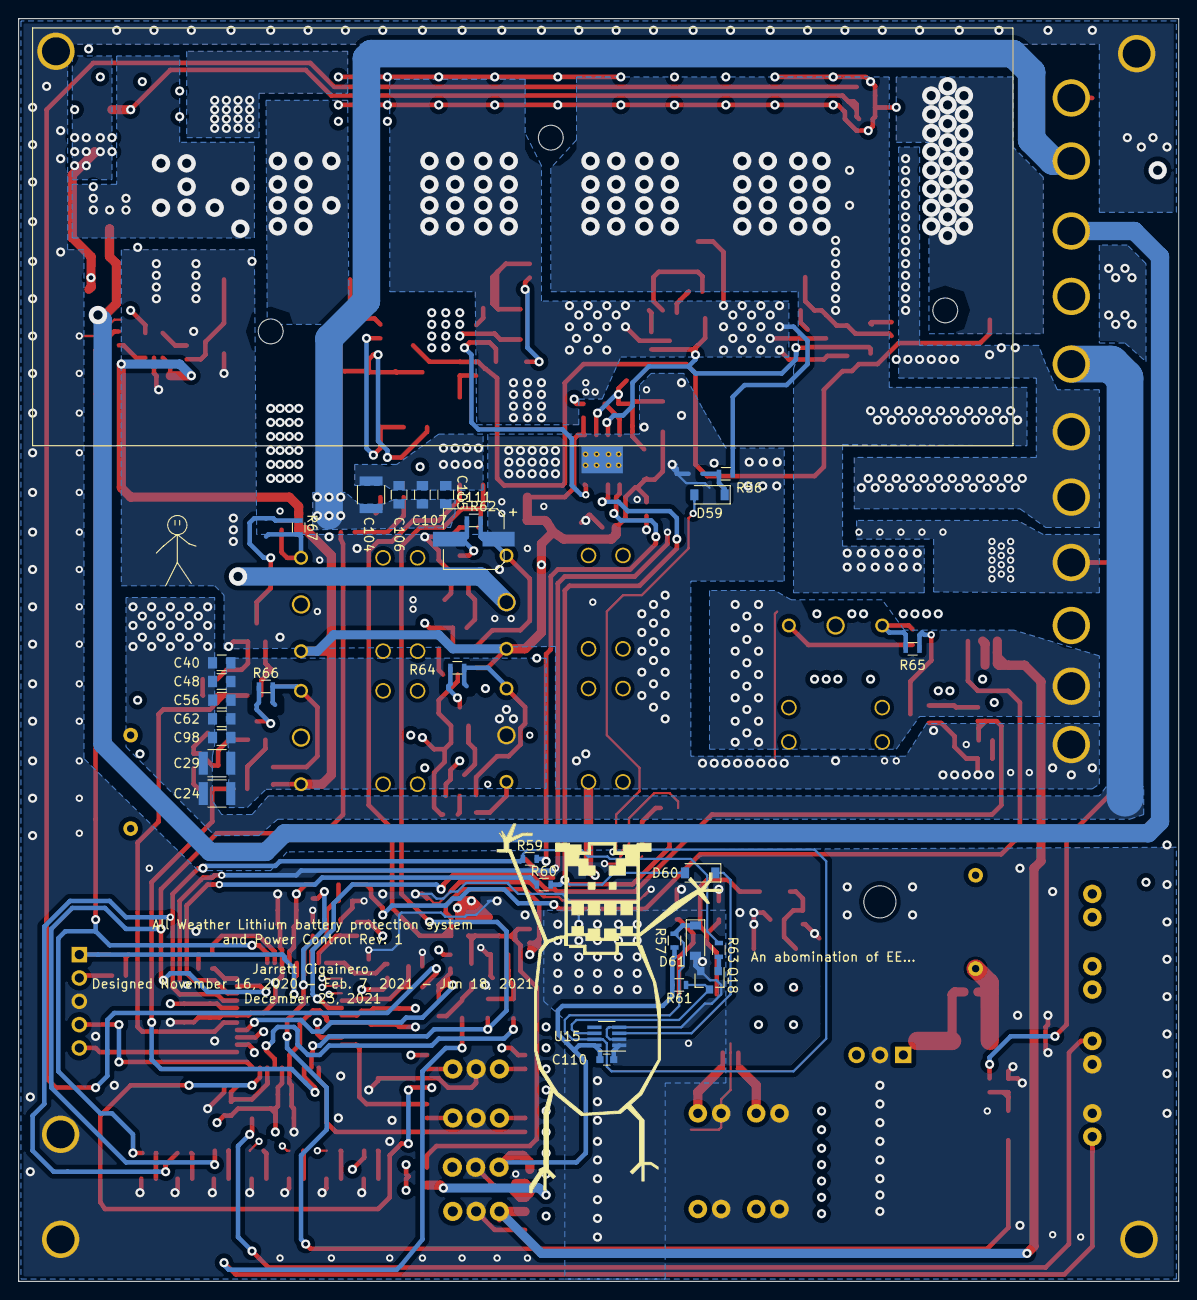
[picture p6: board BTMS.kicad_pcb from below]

Board: 4 copper layers, 126.2 x 137.4 mm, 315 parts (29 on the bottom side), 128 nets.

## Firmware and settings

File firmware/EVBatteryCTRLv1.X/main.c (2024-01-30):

/*Copyright (c) <2024> <Jarrett Cigainero>

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
THE SOFTWARE IS PROVIDED "AS IS", WITHOUT WARRANTY OF ANY KIND, EXPRESS OR
IMPLIED, INCLUDING BUT NOT LIMITED TO THE WARRANTIES OF MERCHANTABILITY,
FITNESS FOR A PARTICULAR PURPOSE AND NONINFRINGEMENT. IN NO EVENT SHALL THE
AUTHORS OR COPYRIGHT HOLDERS BE LIABLE FOR ANY CLAIM, DAMAGES OR OTHER
LIABILITY, WHETHER IN AN ACTION OF CONTRACT, TORT OR OTHERWISE, ARISING FROM,
OUT OF OR IN CONNECTION WITH THE SOFTWARE OR THE USE OR OTHER DEALINGS IN THE
SOFTWARE. */

#include "common.h"

/* Include the Source AND Headers HERE or else mplab gets pissy for some reason.
 * Don't bother trying to include the source and header files into the project,
 * it doesn't work. Either I'm doing it wrong or it's broken, but what I have here WORKS SO DON'T TOUCH IT.
 */

#include "defines.h"
#include "chipconfig.h"
#include "IRQs.h"
#include "sysIRQs.c"
#include "dataIRQs.c"
#include "trapIRQs.c"
#include "common.h"
#include "subs.c"
#include "DataIO.h"
#include "DataIO.c"
#include "Init.h"
#include "Init.c"
#include "display.c"
#include "display.h"
#include "eeprom.c"
#include "eeprom.h"
#include "checksum.c"
#include "checksum.h"
#include "sysChecks.c"
#include "sysChecks.h"
#include "regulate.c"
#include "regulate.h"

/* Program Start */
/***********************************************************
***********************************************************/
int main(void){
    CONDbits.EnableChIRQ = 1;
    /* General 3 IO. */
    GENERAL3_TRIS = 0xFFF1; //set portd to all inputs except for RD2(KEEPALIVE), RD3(UNUSED), and RD1(mainContactor)
    GENERAL3_LAT = 0;
    GENERAL3_PORT = 0;
    keepAlive = 1; //Enable Keep Alive signal. System keeps itself on while main_power is enabled.
    /* Analog inputs and general IO */
    //Initialize PORTB first.
    ANALOG_TRIS = 0x008F;          //set portb to mix analog inputs and digital outputs.
    ANALOG_LAT = 0;
    ANALOG_PORT = 0; //clear portb
    CPUact = 1;             //Turn on CPU ACT light.
    //Calculate space required for eeprom storage.
    cfg_space = sizeof(sets) / 2;
    vr_space = sizeof(vars) / 2;
    dsky_space = sizeof(dsky) / 2;
    //Get variable data if it exists.
    get_variables();
    //Get either default or custom settings.
    get_settings();
    //Do an initial reset and warm start check.
    first_check();
    //Disable Charge Detect IRQ on power up.
    CONDbits.EnableChIRQ = 0;
    //Initialize Systems.
    Init();

/*****************************/
    // Main Loop.
/*****************************/
    /* Everything is run using IRQs from here on out.
     * Look in the other source files that MPLAB doesn't open automatically.
     */
    for (;;)        //loop forever. or not, idc, we have IRQs for stuff.
    {
        //Deep sleep check.
        if(STINGbits.deep_sleep){
            io_off();               //Turn off all IO before sleeping.
            CPUact = 0;      //Turn CPU ACT light off.
            power_off();        //Cuts main power to self.
            /* If the keep alive pin isn't used or if the power control hardware
             * is faulty then this does nothing and the micro will
             * sleep on the next instruction. Even in Sleep it still draws
             * nearly a quarter of a watt! WTF Microchip? Why did I choose
             * this microcontroller again?
             * It's what I had on hand when I first started developing this.
             * Oh well, we have ways of getting around it so it works for now.
             */
            Idle();
            //Sleep();
            STINGbits.deep_sleep = 0;
        }
        else{
            CPUact = 0;      //Turn CPU ACT light off.
            Idle();                 //Idle Loop, saves power.
        }
    }
    return 0;
}

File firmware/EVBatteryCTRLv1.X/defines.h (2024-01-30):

/*Copyright (c) <2024> <Jarrett Cigainero>

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
THE SOFTWARE IS PROVIDED "AS IS", WITHOUT WARRANTY OF ANY KIND, EXPRESS OR
IMPLIED, INCLUDING BUT NOT LIMITED TO THE WARRANTIES OF MERCHANTABILITY,
FITNESS FOR A PARTICULAR PURPOSE AND NONINFRINGEMENT. IN NO EVENT SHALL THE
AUTHORS OR COPYRIGHT HOLDERS BE LIABLE FOR ANY CLAIM, DAMAGES OR OTHER
LIABILITY, WHETHER IN AN ACTION OF CONTRACT, TORT OR OTHERWISE, ARISING FROM,
OUT OF OR IN CONNECTION WITH THE SOFTWARE OR THE USE OR OTHER DEALINGS IN THE
SOFTWARE. */

#ifndef DEFINES_H
#define	DEFINES_H
//##############################################################################
#include <p30f3011.h>
//#include <libpic30.h>
//#include <xc.h>
// Tm = 32767 * (1 / (((clkSpeedmhz * PLL) / 4) / tiksPerIRQ))
//#define IPS 29.48;   //million instructions per second.
#define IPS 14.74   //million instructions per second.
#define BAUD1 9600  //Default BAUD rate for PORT 1
#define BAUD2 9600  //Default rate for PORT 2
#define calc_125 0.00003472 //Value for calculating the total current in and out of battery every second.
//Firmware Version String
#define version "\n\rV1.0A\n\r"
//IO inputs
#define keySwitch !PORTFbits.RF1
#define chrgSwitch PORTEbits.RE8
//Analog inputs
#define adcVoltage ADCBUF0 //Voltage
#define adcCurrent ADCBUF1 //Current
#define adcBTemp ADCBUF2 //Batt Temp
#define adcMTemp ADCBUF3 //Motor Temp
#define adcSTemp ADCBUF4 //Self Temp
//IO outputs
#define CPUact LATBbits.LATB6
#define errLight LATBbits.LATB5
#define chrgLight LATBbits.LATB4
#define keepAlive LATDbits.LATD2
#define fanRelay LATFbits.LATF0
#define heatRelay LATCbits.LATC15
#define AUXrelay LATBbits.LATB8
#define ctRelay LATDbits.LATD1
#define chrgRelay LATFbits.LATF6
#define outPWM PDC3
#define heatPWM PDC1
#define chrgPWM PDC2

//IO
#define ANALOG_TRIS TRISB
#define ANALOG_LAT LATB
#define ANALOG_PORT PORTB

#define GENERAL1_TRIS TRISC
#define GENERAL1_LAT LATC
#define GENERAL1_PORT PORTC

#define GENERAL3_TRIS TRISD
#define GENERAL3_LAT LATD
#define GENERAL3_PORT PORTD

#define PWM_TRIS TRISE
#define PWM_LAT LATE
#define PWM_PORT PORTE

#define GENERAL2_TRIS TRISF
#define GENERAL2_LAT LATF
#define GENERAL2_PORT PORTF

//Memory Defines
/* This assums the compiler puts the stack at the end of memory space just after
 * the user variables and the stack pointer counts up */
#define ramSize 0x03FF
#define ramAddressStart 0x0800
#define stackFaultDefault ramSize + ramAddressStart
#define ramFree (ramSize + ramAddressStart) - 15 //Minus 15 bytes of ram. If the stack intrudes on this then it should throw an error code before a complete system crash.

//General
#define yes 1
#define no 0
#define on 1
#define off 0
#define set 1
#define clear 0
#define NULL 0
#define input 1
#define output 0

//Heater calibration
#define notrun 0
#define initialize 1
#define calibrating 2
#define ready 3
#define error 4
#define disabled 5

//##############################################################################
#endif

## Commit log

2021-06-18 Initial Commit and Upload of BTMS Rev. 1
    [BTMS.kicad_pcb, BTMS.sch]
2021-06-18 Reorganized files.
    [BTMS.kicad_pcb, BTMS.sch]
2021-06-18 Deleted outdated board renderings.
2021-06-18 Updated KICAD custom parts.
    [BTMS.sch]
2021-06-18 Created PDF schematic and updated Silkscreen on board layout.
    [BTMS.kicad_pcb]
2021-06-18 Updated board layout to reflect schematic.
    [BTMS.kicad_pcb]
2021-07-03 Updated silk screen placement for some parts.
    [BTMS.kicad_pcb]
2021-08-07 Updated parts list. Updated Gerber files. Updated board to reflect schematic. Tweaked some parts of the schematic.
    [BTMS-B_Cu.gbr, BTMS-B_Mask.gbr, BTMS-B_SilkS.gbr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]
2021-08-08 Updated U3 to reflect proper pinout for UCC27201DDAR
    [BTMS.kicad_pcb, BTMS.sch]
2021-08-08 Updated PDF to reflect schematic changes.
2021-12-17 Cleaned up some corners on PCB layout. I don't like the main buck converter half bridge design. Might change later. Still Need To Test This Revision.
    [BTMS.kicad_pcb]
2021-12-24 Cleaned up a few things. Added mosfet to help protect against both high and low side fets from being on at the same time. Generated Gerber Files. Getting ready to fabricate this board and begin testi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
    [BTMS-B_Cu.gbr, BTMS-B_Mask.gbr, BTMS-B_SilkS.gbr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]
2022-01-02 Updated firmware for schematic changes. Getting ready to test new design for the first time.
    [BTMS.kicad_pcb]
2022-01-02 Refactored and optimized fault code readout routine. <-Need to test this once boards are assembled and functioning.
2022-01-03 Added Digikey parts list. Ordered parts, but many critical parts are on backorder so I will be reusing parts from the older prototypes that didn't explode.
    [BTMS.sch, digikeyPartsList.csv, digikeyPartsList.xlsx]
2022-02-13 Began board design bug fixes and upgrades. Began implementing vehicle speed calculation routines. Fixed a bug where system would power itself off 1 sec after unplugging charger. Fixed a bug where hea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
    [BTMS.kicad_pcb, BTMS.sch, supplementedParts.csv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]
2022-02-14 Removed R58 from circuit design; not needed. Changed firmware to use built in dead time generator and verified that the High and Low differential pair is configured correctly. Circuit seems to work a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
    [BTMS.kicad_pcb, BTMS.sch]
2022-02-14 Added some pictures of the test board.
2022-02-14 Updated battery voltage divider.
    [BTMS.sch]
2022-02-14 Fixed a mislabeled net; changed from 5vP to 5vC on U4. Need to update board layout; changed some capacitors and other previously noted schematic changes.
    [BTMS.sch]
2022-02-16 Refactored Command Interpreter code and Serial port code to allow multi-tasking. FIXME: serial console is buggy but mostly functional for some reason. Too tired to fix it right now.
    [DataIO.h, Init.c, errorCodes.h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]
2022-02-16 Fixed buggy serial port stuttering and garbage data.
    [Init.c, subs.c]
2022-02-18 Fixed EEPROM storage so that it works now. Added system for checking Program memory checksum and EEPROM checksum.
    [DataIO.h, Init.c, errorCodes.h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]
2022-02-20 Updated readme to list current state of project.
    [BTMS.kicad_pcb, BTMS.sch]
2022-02-25 Major refactoring, and optimizations. Added some groundwork for custom serial port displays. NEW BUGS: Serial ports hang for some unknown reason. Heatcal gets ran multiple times when charger is plugg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
    [BTMS.sch]
2022-02-26 Refactored charge detect and regulation routines.
    Fixed some bugs with the heat control and calibration. Heat cal only runs once when starting from cold and dead, but no implementation for running heat cal on warm start charger plugin. <- TODO
    Serial port still hangs sometimes.
    [Init.c, common.h, regulate.c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]
2022-02-26 Added routines in the heart beat IRQ to check for serial port buffer overflow, log an error code, and clear the buffer if detected. Also changed
    checksum timer IRQ priority to 1 as I think that is what was causing the receive IRQ to hang during high CPU loads. Will test tomorrow.
    [Init.c, errorCodes.h, sysIRQs.c]
2022-02-27 A little bit of refactoring. A few minor bug fixes and adjustments of code. System now adjusts current linearly from battery temperature limits rather than hard coded arbitrary % current set points. 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
    [DataIO.h, Init.c, common.h]
2022-03-12 Fixed bug where charge current detect timeout wouldn't time out.
    [Init.c, common.h, regulate.c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]
2022-06-12 Updated prototype HUD routines to work and be configurable. Need to implement system config upload/download routines. Fixed bug where not all settings or variables would be correctly saved to or retr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
    [DT80.kicad_pcb, DT80.sch]
2022-06-13 Updated Commands list. Fixed a bug with HUD custom data not working. Heater cal bug where heater cal runs after reset even though it's set to disabled has reappeared. Added Version String command.
    [DataIO.h, Init.c, common.h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]
2022-06-13 Moved HUD display to Timer 5 with a low priority IRQ.
2022-06-13 Updated timer 5 IRQ priority. Changed default HUD config to work with display that I have.
2022-06-15 Refactored some code. Fixed serial ports interfering with each other.
    [DataIO.h, Init.c, common.h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]
2022-06-15 Refactored analog input routines. Fixed bug where open circuit voltage routines would not get the correct voltages.
    [Init.c, common.h, subs.c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]
2022-09-14 Fixed bug where a shutdown and insufficient current error would be logged even when the charger was working.
    [Init.c, regulate.c]
2024-01-30 Changed licensing of firmware from GNU to MIT.
    [DT80.kicad_pcb, DT80.sch]
